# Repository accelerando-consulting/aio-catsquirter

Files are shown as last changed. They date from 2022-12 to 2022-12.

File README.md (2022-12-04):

# CatSquirter - a mosfet switching shield for pumps or other small loads

This project is a circuit board that allows one to control a high current
output using a Mostfet rather than a relay.  It is intended to stack atop the
Lolin D1 mini microcontroller board, or any other board that uses the D1 bus (such as 
Accelerando Redsoil (nRF52840) , Accelerano Bungan (nRF52833) or Accelerando Cowan (ESP32-C3).

It was originally created to drive a small submersible fountain pump in order to produce a brief
spray of water (harmless but surprising) to discourage a pet from scratching an item of furniture.

## How it works

Jumpers allow any of D0,D1,D5-D8 to be connected to the gate of the MOSFET.  When the corresponding pin is
HIGH, the MOSFET turns on and power flows to the PUMP socket. 

Another jumper controls the source of the power to the pump.   For a battery operated pump, fit a Lolin battery shield and
connect the battery to the catsquirter shield, then connect the second battery connector to the Lolin shield.   This
arrangement uses the high current available direct from a lithium battery to run the pump.

Alternatively, if your project is not battery powered, a jumper allows connecting the 5v or 3v3 pins from the
D1 stacking bus to the mosfet drain.  (Be careful not to use more current than your regulator can handle!).   In one
instance I'm using the 5v from the USB connecter to run a small vacuum pump.

Finally, if you have a higher voltage load (say, 12v), you could connect power to one of the battery headers (in which case DO NOT connect the second header to a battery shield!).

A LED will light when the pump fet is enabled.

## What can I do with it

* Water your indoor pot-plants.
* Control a low voltage cooling or ventilation fan
* Make a small drinking fountain for people or pets.
* Run a vacuum pump or fume extractor for soldering.
* Stack several of these (with different jumper settings on each one) to control several devices.
* Control low voltage LED lighting (up to 2A, for higher current lighting see Accelerando Jahlo).
* Control a heavy duty relay for more signifiant loads

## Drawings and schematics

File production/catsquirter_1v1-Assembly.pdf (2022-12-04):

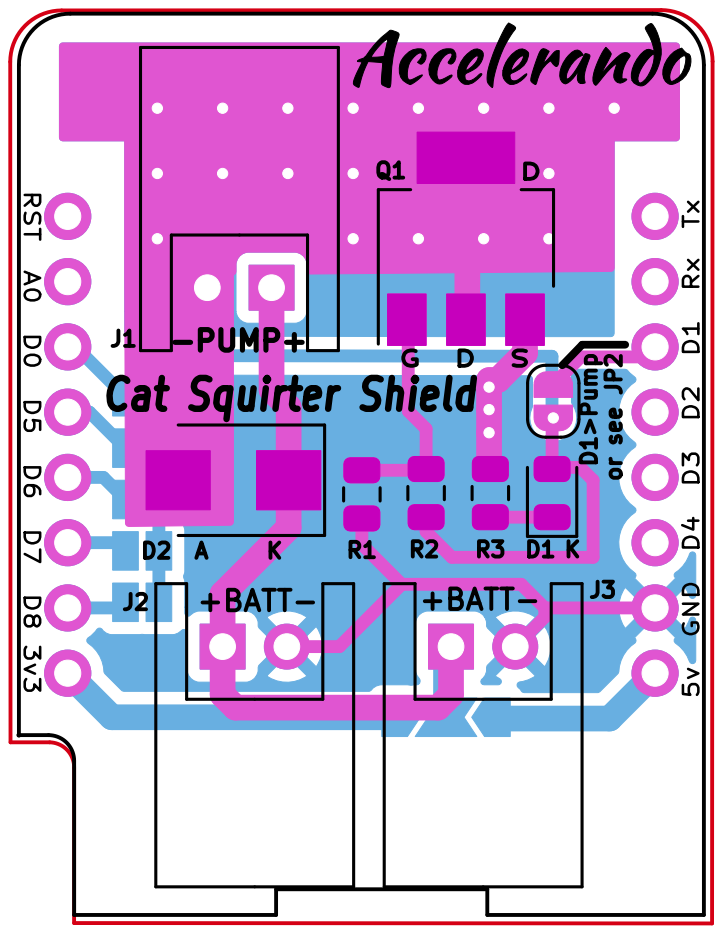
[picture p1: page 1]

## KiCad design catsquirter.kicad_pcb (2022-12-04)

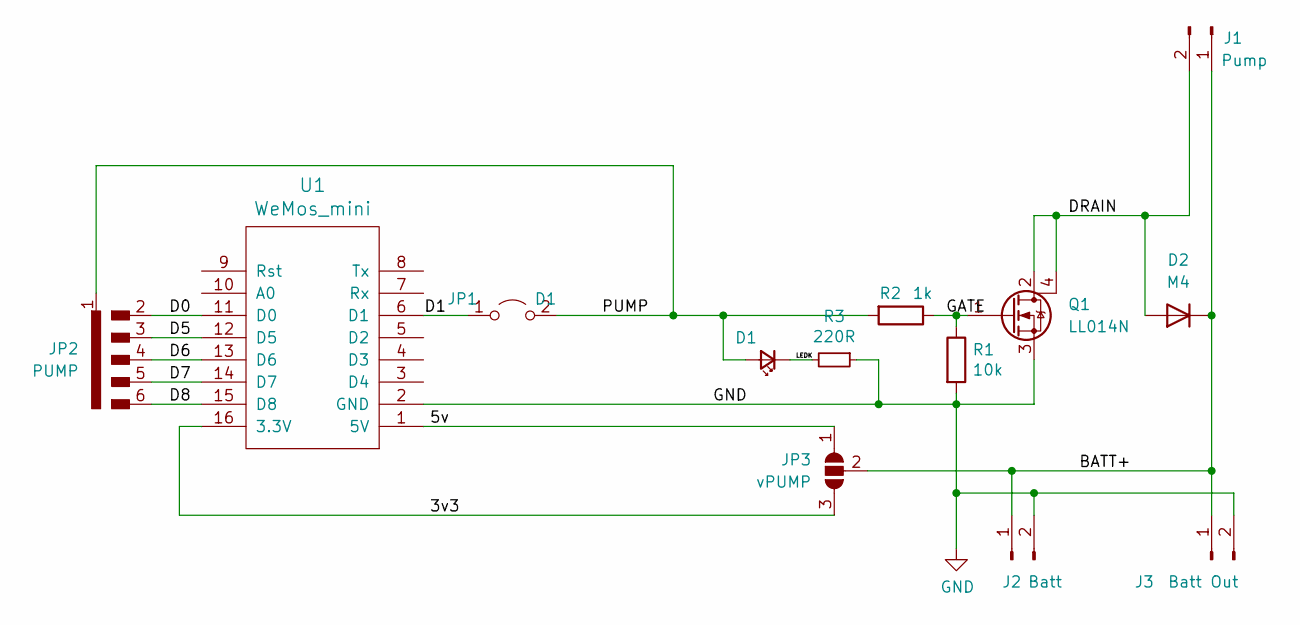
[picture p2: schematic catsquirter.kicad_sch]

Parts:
D1: LED_Small; LED_0805_2012Metric
D2: M4; D_SMB
J1: Pump; JST_XH_S02B-XH-A_02x2.50mm_Angled
J2: Batt; JST_XH_S02B-XH-A_02x2.50mm_Angled
J3: Batt Out; JST_XH_S02B-XH-A_02x2.50mm_Angled
JP1: D1; SolderJumper-2_P1.3mm_Open_RoundedPad1.0x1.5mm
JP2: PUMP; SolderJumper-5_P1.3mm_Open_Pad1.0x1.5mm
JP3: vPUMP; SolderJumper-3_P2.0mm_Open_TrianglePad1.0x1.5mm
Q1: LL014N; SOT-223
R1: 10k; R_0805_2012Metric
R2: 1k; R_0805_2012Metric
R3: 220R; R_0805_2012Metric
U1: WeMos_mini; wemos-d1-mini-connectors-only

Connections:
/3v3: JP3.3 (B), U1.16 (3.3V)
/5v: JP3.1 (A), U1.1 (5V)
/BATT+: D2.1 (K), J1.1, J2.1, J3.1, JP3.2 (C)
/D0: JP2.2 (A), U1.11 (D0)
/D1: JP1.1 (A), U1.6 (D1)
/D5: JP2.3 (B), U1.12 (D5)
/D6: JP2.4 (C), U1.13 (D6)
/D7: JP2.5 (D), U1.14 (D7)
/D8: JP2.6 (E), U1.15 (D8)
/DRAIN: D2.2 (A), J1.2, Q1.2 (D), Q1.4 (D)
/GATE: Q1.1 (G), R1.1, R2.1
/LEDK: D1.1 (K), R3.2
/PUMP: D1.2 (A), JP1.2 (B), JP2.1 (A), R2.2
GND: J2.2, J3.2, Q1.3 (S), R1.2, R3.1, U1.2 (GND)

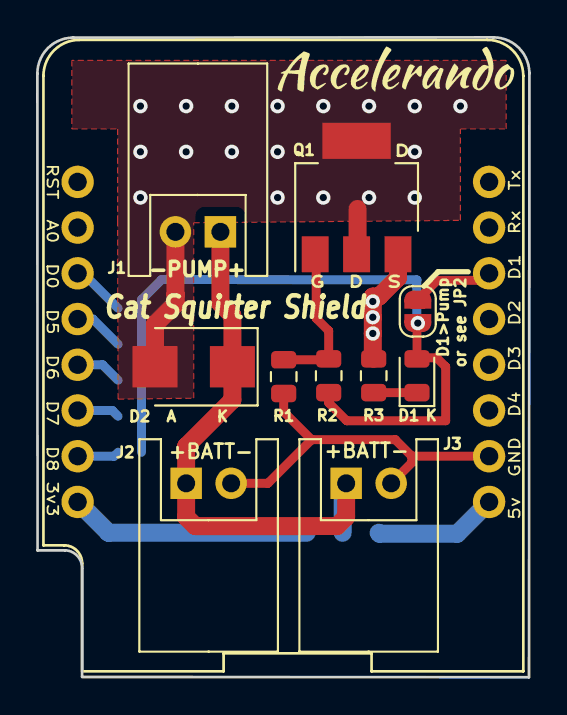
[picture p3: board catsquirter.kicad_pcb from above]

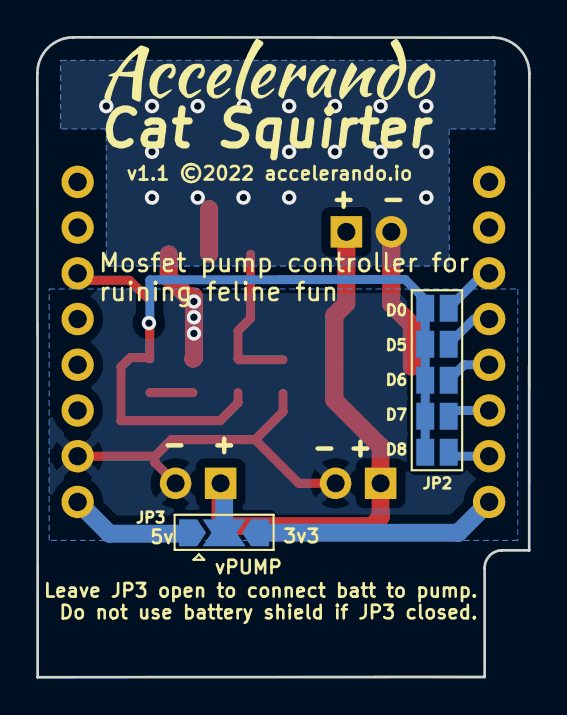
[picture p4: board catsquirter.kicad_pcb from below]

Board: 2 copper layers, 27.3 x 35.5 mm, 13 parts (2 on the bottom side), 14 nets.

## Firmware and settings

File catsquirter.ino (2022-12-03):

#define BUTTON_PIN 17
#define PUMP_PIN 16

void setup() {
  Serial.begin(115200);
pinMode(PUMP_PIN,OUTPUT);
digitalWrite(PUMP_PIN,0);
pinMode(BUTTON_PIN,INPUT_PULLUP);
Serial.println("pump up the jam");

}

void loop() {
  // put your main code here, to run repeatedly:
  static bool pump = LOW;
  
  if (digitalRead(BUTTON_PIN)==LOW) {
    // button is connected to ground (LOW) when pressed, pulled up high when not pressed
    digitalWrite(PUMP_PIN,HIGH);
    if (pump != HIGH) {
      Serial.println("on");
      pump = HIGH;
    }
  }
  else {
    digitalWrite(PUMP_PIN, LOW);
    if (pump != LOW) {
      Serial.println("off");
      pump = LOW;
    }
  }
}

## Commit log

2019-09-14 D1 shields for various client projects
    [d1_mosfet_hat.kicad_pcb, d1_mosfet_hat.sch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]
2022-04-12 d1_mosfet shield v1
    [d1_mosfet_hat.kicad_pcb, d1_mosfet_hat.sch]
2022-04-12 Remove unwanted files
    [d1_mosfet_hat-B.Cu.gbr, d1_mosfet_hat-Edge.Cuts.gbr, d1_mosfet_hat-NPTH.drl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]
2022-12-03 Cat squirter v1.1 - add jumpers to use 5v or 3v power
    [d1_mosfet_hat.kicad_pcb, d1_mosfet_hat.kicad_sch, d1_mosfet_hat.sch]
2022-12-04 Add pin/volt jumpers. Rename project files d1_mosfet_hat -> catsquirter.
    [catsquirter.kicad_pcb, catsquirter.kicad_sch, d1_mosfet_hat.kicad_pcb]
2022-12-04 Gerbers for catsquirter 1v1
    [catsquirter.kicad_pcb]

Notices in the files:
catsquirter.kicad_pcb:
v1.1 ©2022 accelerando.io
